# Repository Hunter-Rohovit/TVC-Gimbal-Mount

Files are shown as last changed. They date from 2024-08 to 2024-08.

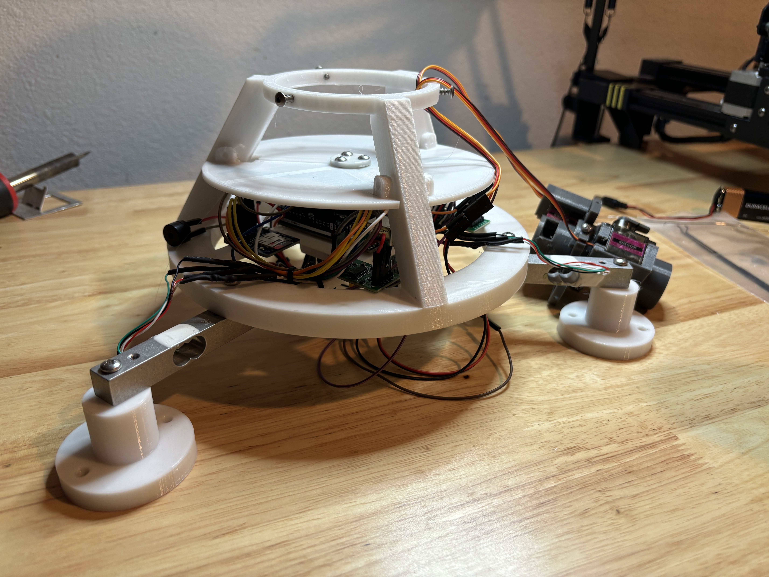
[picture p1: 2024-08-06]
TVC Mount Pics/ElectronicsShield(4).jpg

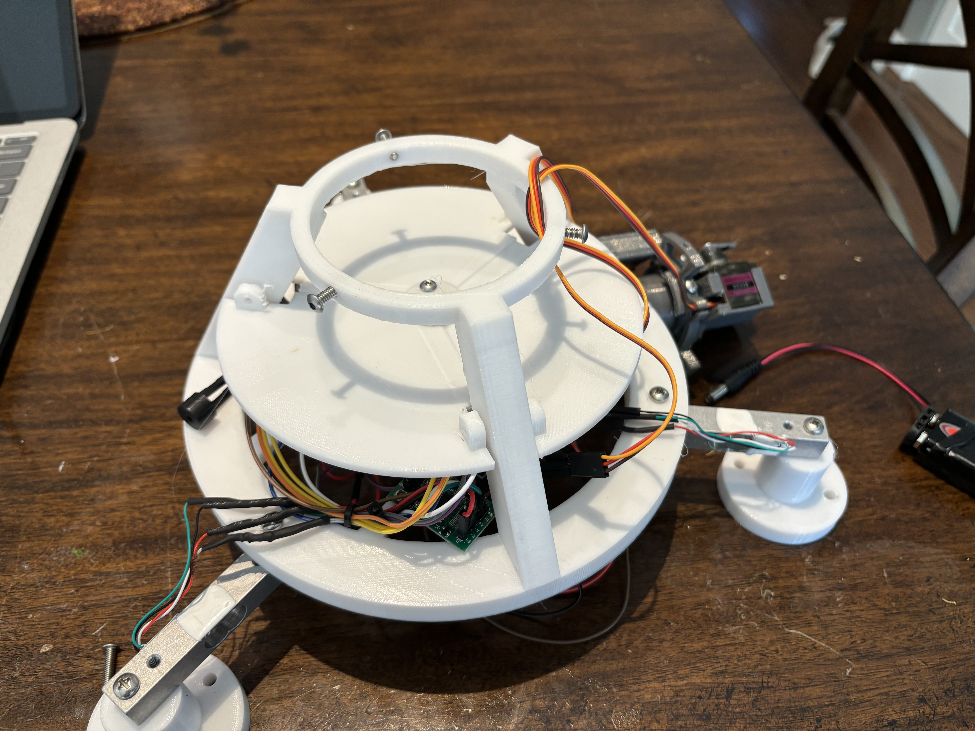
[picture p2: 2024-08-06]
TVC Mount Pics/ElectronicsShield.jpg

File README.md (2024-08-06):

# TVC-Gimbal-Mount
The TVC Gimbal Mount is an ongoing project with the eventual goal of creating a model rocket entirely controlled by TVC. This project was inspired by Joe Barnard @BPS.space, who attempted to land a model rocket using TVC. As for right now, the only goal is to achieve vertical controlled liftoff. The gimbal mount is designed using Autodesk Fusion360 to be 3D printed in three main pieces (outer layer, inner layer, motor casing). The current version is capable of 10 degrees of freedom. While designing an effective TVC mount is the main goal of the project, I am also gaining valuable experience with collecting data and performing data analysis on Static Fire tests. Most of the data being collected is thrust-force produced by the solid rocket motors through the use of load cells and HX711 amplifiers. This project ultimately is a culmination of all the skills I have learned so far and is purely my design: CAD, Arduino, Python. [Link to Onshape CAD model](https://cad.onshape.com/documents/d0d010f00d2c0b7870c7f789/w/7c25825be46c67b1ea6ad60a/e/3f60fee57cc94159316f0923)

## Static Fire Test


## TVC Mount


## CAD Design


## Data Analysis


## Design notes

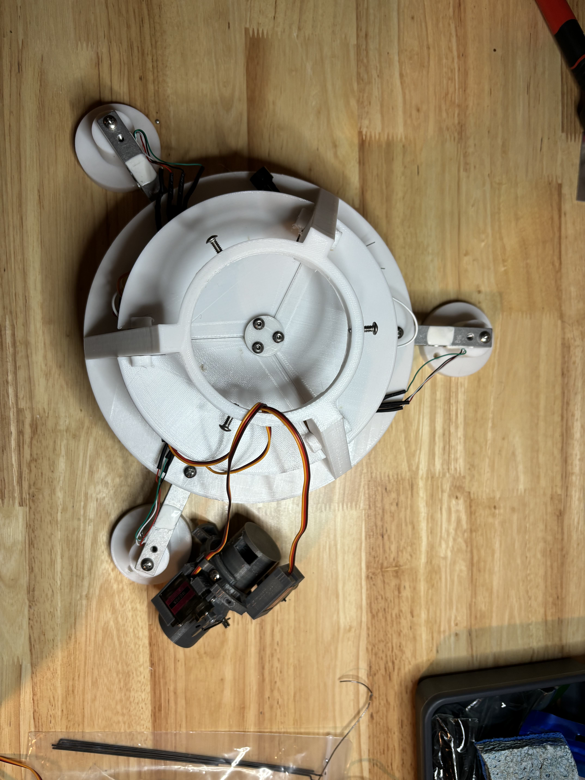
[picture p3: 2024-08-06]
TVC Mount Pics/ElectronicsShield(3).jpg

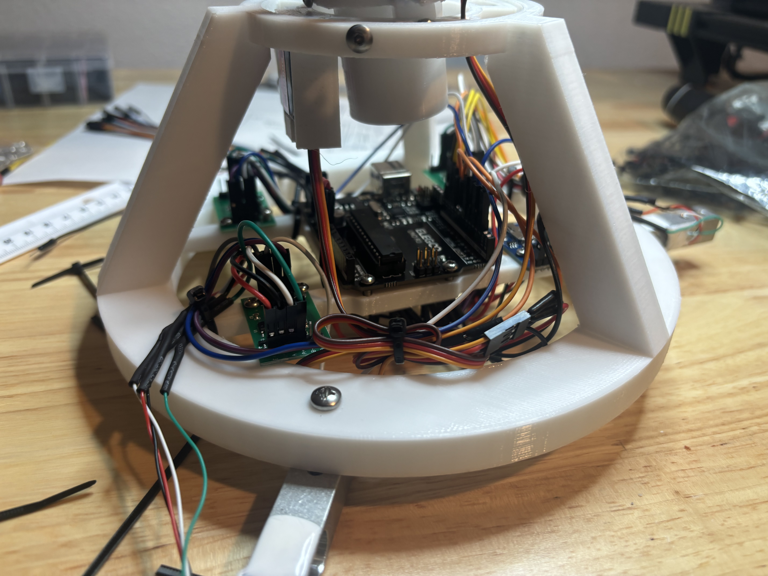
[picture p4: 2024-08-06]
TVC Mount Pics/Electronics(3).jpg

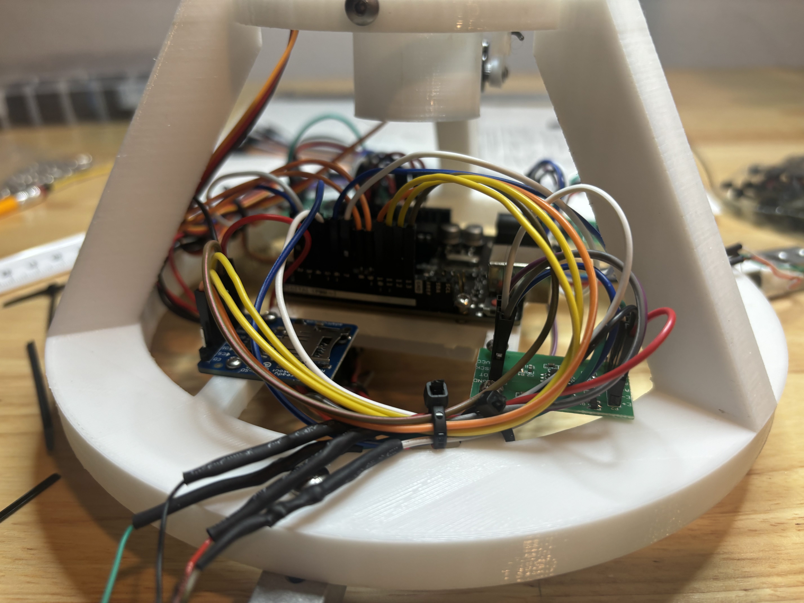
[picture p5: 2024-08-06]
TVC Mount Pics/Electronics(2).jpg

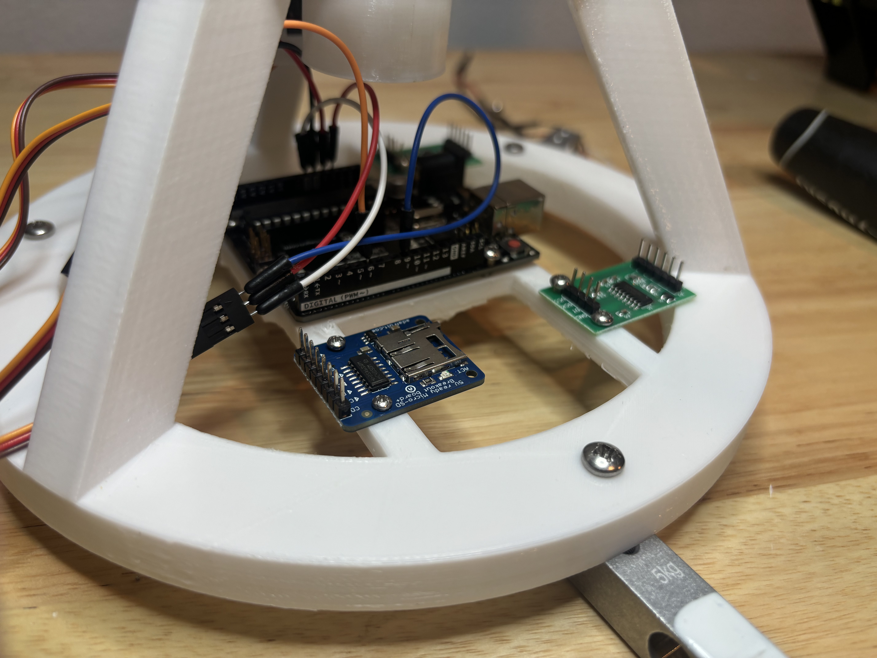
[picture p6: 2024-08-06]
TVC Mount Pics/Electronics(NotConnected).jpg

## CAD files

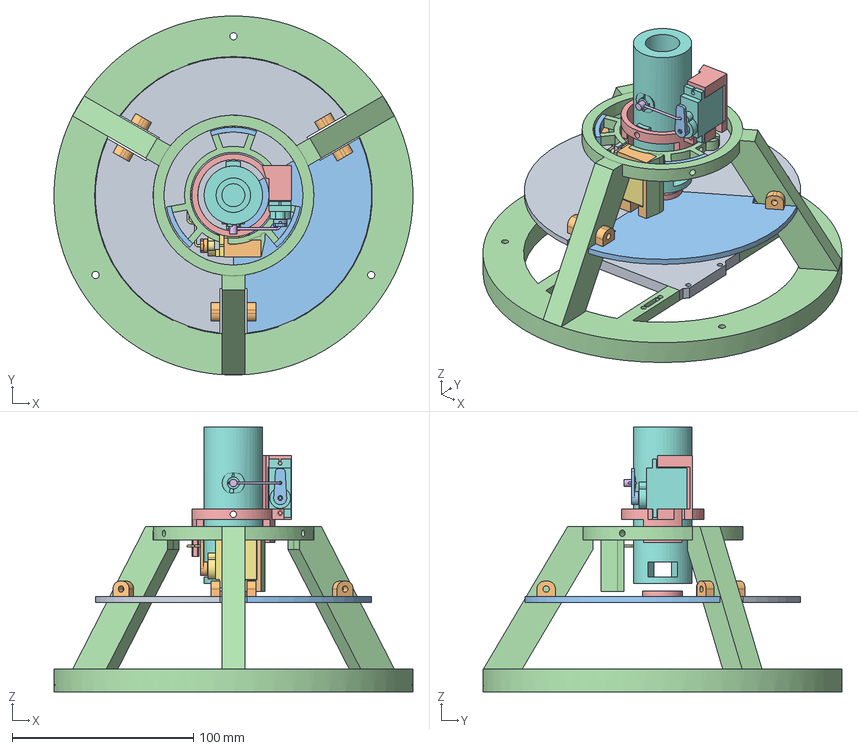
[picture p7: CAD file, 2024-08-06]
CADfiles/TVC_FullTestMount.step
197.9 x 197.9 x 146.1 mm
InnerLoop(Mirror)
InnerLoop
InnerLink
OuterLink\
C6-5 Engine Holder
ArduinoPlate
Thread
Thread (1)
ShieldPt2
Thread (2)
Thread (3)
StaticFireMount (1)
ShieldConnector
LinkageStopper
OuterServo
Thread (4)
InnerServo
Thread (5)
ShieldPt1
OuterControlHorn
InnerControlHorn

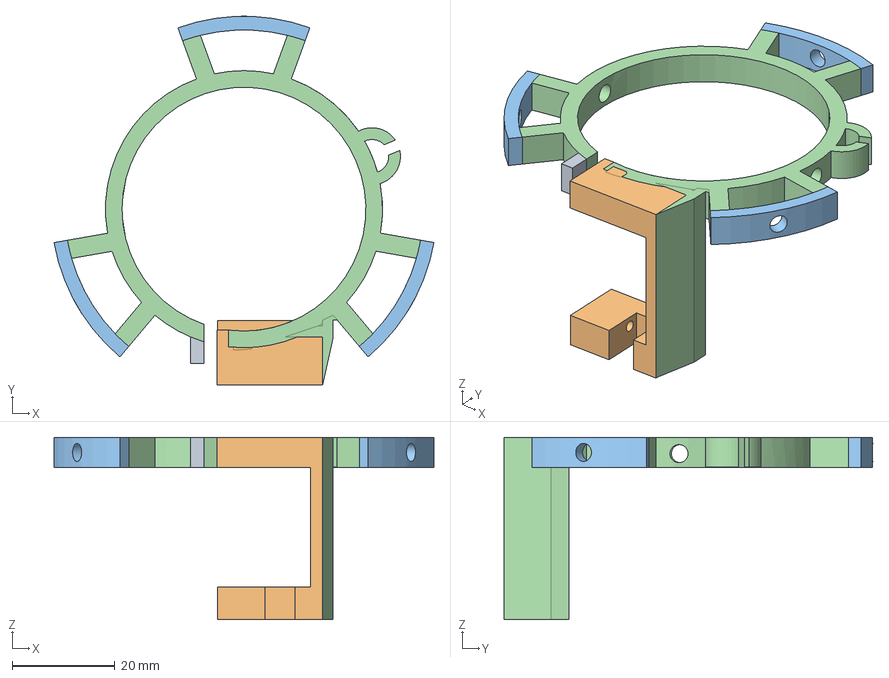
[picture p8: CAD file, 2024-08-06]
CADfiles/OuterLoop.step
73.8 x 71.6 x 35.4 mm
InnerLoop(Mirror)

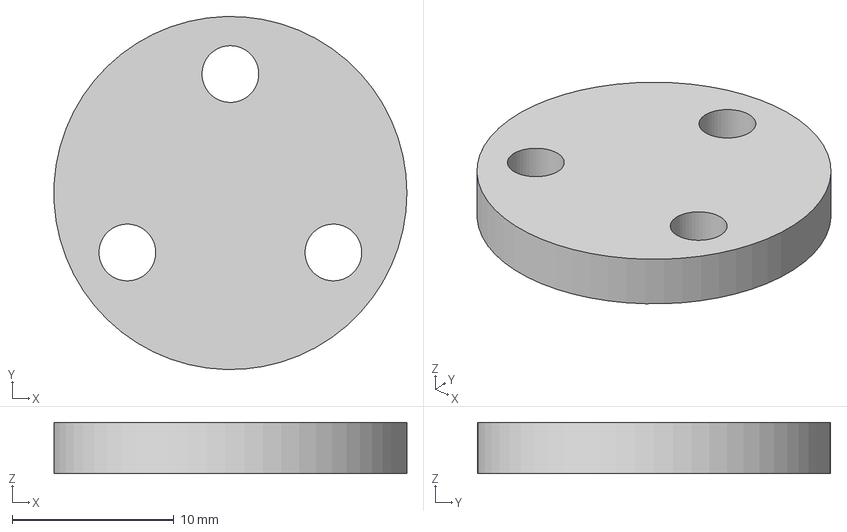
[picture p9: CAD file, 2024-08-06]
CADfiles/ShieldConnector.step
21.8 x 21.8 x 3.17 mm

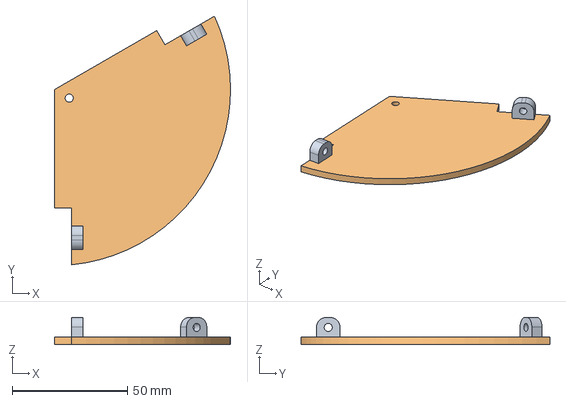
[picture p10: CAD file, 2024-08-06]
CADfiles/Electronics Shield.step
76.2 x 107.6 x 11.7 mm

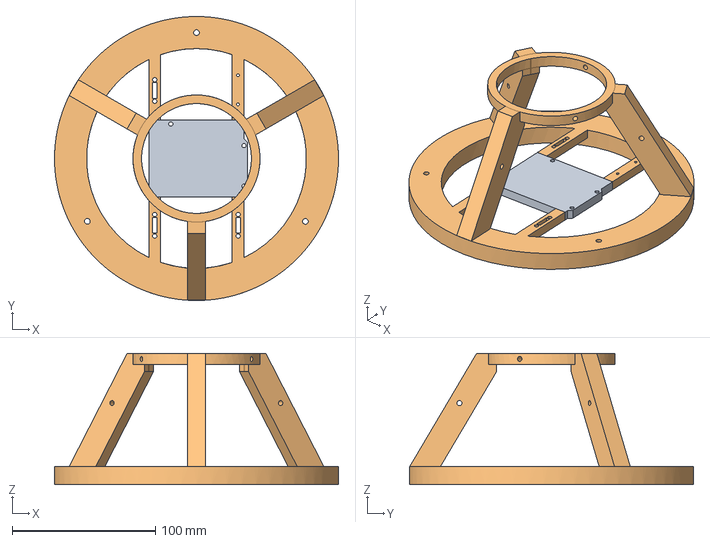
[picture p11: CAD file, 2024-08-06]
CADfiles/StaticFireMount.step
197.9 x 197.9 x 91.4 mm

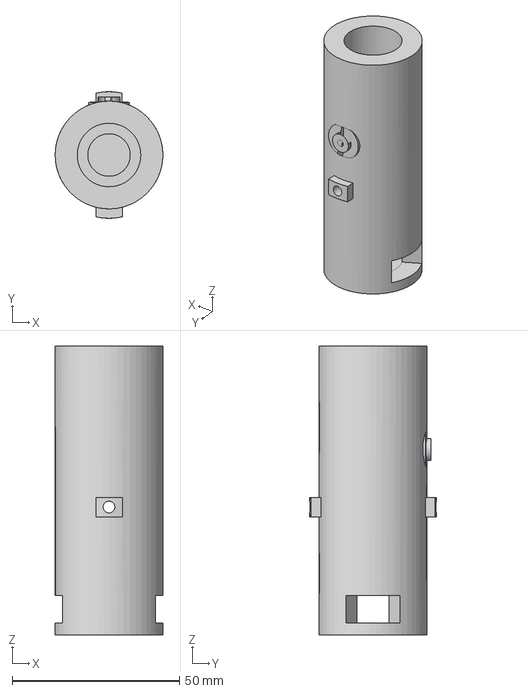
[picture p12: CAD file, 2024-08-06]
CADfiles/MotorHolder C6-5.step
32.2 x 37.8 x 86.4 mm

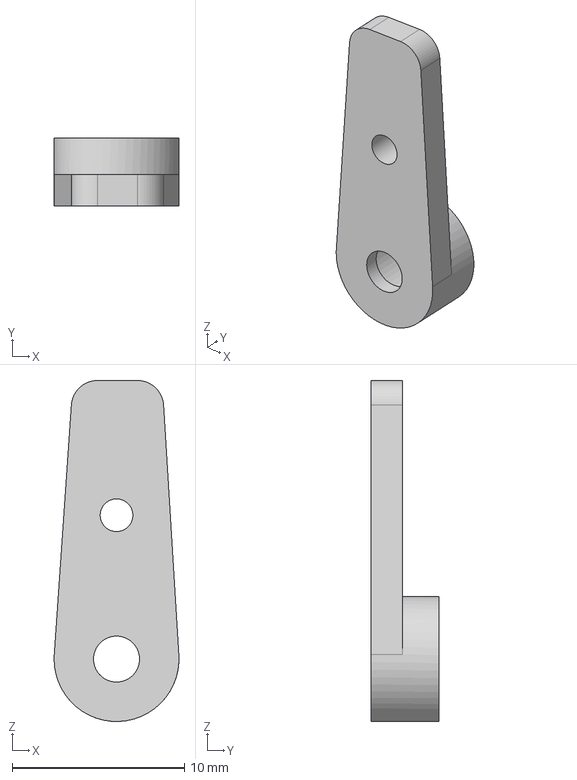
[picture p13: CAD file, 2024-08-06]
CADfiles/Control Horn Upper.step
7.25 x 3.96 x 19.8 mm

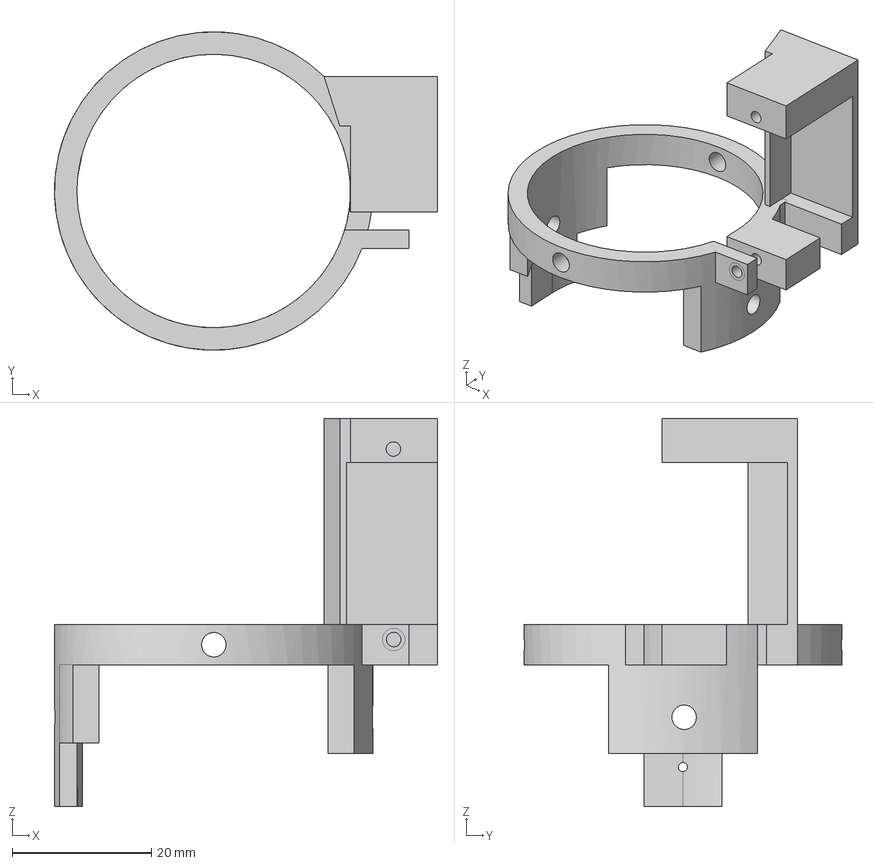
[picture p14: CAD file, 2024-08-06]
CADfiles/InnerLoop.step
55.0 x 45.7 x 55.8 mm

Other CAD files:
CADfiles/ControlHornLower.step

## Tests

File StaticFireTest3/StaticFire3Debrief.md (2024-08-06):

Static fire 3 was the most successful test so far. No critical errors involved. TVC mount control significantly improved compared to last test. Little to none unwanted movement with the outer servo. Likely a result of improvements with the TVC mount itself. Less stripped hinge damped any minor movements in the servo and smaller hole for servo link prevented any wiggle movement. Although there is still improvement to be made with servo control, this test showed positive signs. TVC stayed vertical when it was supposed to with little sporadic movement. The four corner gimbal worked very well again. After the mount completed its four corner gimbal, it returned to its original zero position. The total impulse (8.23N) was again lower than the expected impulse of 10N. I recalibrated the load cells using an actual scale compared with my previous weight of water method (poured 500ml of water into a cup on the scale and set the known weight to be 500g). To my surprise there wasn't a large difference in thrust values. However, my max thrust was significantly higher at 13.8N. At this point, I believe the lower thrust is not a result of improperly calibrated loadcells, but rather manufacturer's error in making the solid rocket motors. Another test might be needed to be confident with this assumption though.

Looking at the Thrust vs. time graph, the 80hz load cells again created a more detailed graph. The max thrust was at 13.82N, which is the highest so far. However, the total impulse was the lowest its been so far at 8.23N.

Looking at the scatterplot is where we find the most significant improvements from the test. The x-range was only 3.22cm and the y-range was 2.99cm. The fact that these two values are nearly identical and relatively small in magnitude shows that both the inner servo and the outer servo have good control of the motor holder. Compared to the last few tests where one of the ranges was always significantly greater than the other.

After Static Fire 3 I decided to improve the graphs/plots in DataPlotter.py through the use of animations. For the Thrust vs. time graphs I added a vertical line that shades in the graph as it moves from left to right. Although there isn't a very practical application to this vertical line, it is definitely more visually appealing. However, in the scatter plot showing the center of force, I decided to plot the points one-by-one with time. Now, it is easy to see how the center of force actually moved with respect to time. Because flight test 3 made use of the four corner gimbal, we can actually see the movement of the TVC in the scatter plot. The scatter plot creates a "diamond" shape, which makes sense as the TVC moved to four different corners. We can also see that after the "diamond" shape is created, data points are plotted at the center of the diamond, which aligns with the code moving the TVC mount back to the center or zero positions. Additionally, since the time of the scatter plot is aligned with the time of the Thrust graph, we can see that the four corners movement started at approximately 0.2s past the time where Thrust = 1N, which verifies the TVC code worked as intended. 

Overall, a very successful test. Greater control over thrust vectoring and systems working as intended. New changes to DataPlotter code provide better analysis of collected data. At this point, it is unlikely there will be any major changes to the TVC mount. Possibly minor changes to hinge width or servo link hole sizes. Minor changes to electronics and power distribution are also possible. Additionally, converting the electronics into a PCB is likely a next step for the static fire mount. However, after these past tests, it is likely I will begin working on the actual rocket itself and flight software to reach the ultimate goal of a thrust vector controlled rocket.  
<br>
<br>
Changes for test 4:<br>
-TBD <br>

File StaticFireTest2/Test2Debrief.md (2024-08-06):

Another successful test of the TVC mount without any critical errors involved. TVC mount didn't break this time as a result of increased strength from PETG and widened hinges. Ejection vents worked flawlessly and electronics shield prevented any flames from reaching the electronics beneath it. TVC mount struggled to stay vertical when it was supposed to. Lots of sporadic movement, mostly with the outer servo. The four corner gimbal worked very well (much better than I had anticipated). The TVC mount appeared to be more in control during gimbaling movements rather than during static positions. The force from the thrust didn't affect the servos ability to move the motor holder in both directions. The total impulse (8.54 N-s) was significantly lower than the expected impulse of 10 N-s. However, it was similar to the previous test of 8.76 N-s. I didn't recalibrate the load cells to see if the calibration factors were truly the issue. However, considering both tests had similar total impulse that were both lower than expected yield, I am confident that the load cells just need to be recalibrated. 

Looking at the Thrust vs. time graph, we can see the 80hz load cells provided a much cleaner and more detailed graph than the 10hz load cells (obviously 8 times the amount of data would do this). This time max thrust was 11.175N which is more than the previous test's. However, because the last test was recorded at 10hz it is likely the true max wasn't recorded in the data. After the initial peak thrust, there is constant thrust at around 4N for the next 1.6 seconds. Once again, this graph matches up with the manufacturer's data. 

Looking at the scatterplot, we can visibly see that the TVC mount was less controllable during this test. The max Y-range was 67.5cm, which is definitely a recording error as the max it can be is 14cm. More analysis of the data is needed to get rid of outlier data. The range in the X-direction was 6cm which is reasonable. The excessively large range in the y-direction shows the lack of control with the outer loop. Considering the servo pulls on the inner loop with a larger lever arm, the servo has to move significantly less to move the mount the same number degrees as compared with the inner servo which pulls directly on the motor holder. 

Considering the changes that were made with test 2 and the sporadic movement of the servos that wasn't seen with test 1, it is safe to say the movement has to do with changing the HX711 boards from 10hz to 80hz. These boards pull significantly more current than they did in test 1 leaving the servos with insufficient power. I attempted to resolve this issues in multiple ways. The first was adding a power supply solely for powering the servos. This improved the servos' ability to gimbal, but it didn't prevent the sporadic movement during static holds. (I made sure to connect the power supply's ground to the Arduino's ground, so as to have a common ground) The next idea I had was to connect a 1000uF capacitor in parallel with the servos' power and ground wires. I figured the capacitor's ability to store charge would help smooth the current creating a more stable TVC mount, but nothing changed after implementing this. I tried replacing the motors, which did help a little bit, but not much. I also made sure the 9V batteries that were used were full, but that also had little effect. In conclusion, I am not sure how to move forward with making the TVC mount more stable. But, I'm fairly confident it is a power distribution issue rather than a mechanical or coding error. 
<br>
<br>
Changes for test 3: <br>
-recalibrated load cells <br>
-Smaller hole size for outer servo link<br>
-less stripped outer hinge<br>

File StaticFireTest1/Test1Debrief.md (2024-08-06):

Overall a successful first test. TVC mount stayed vertical throughout the duration of the test. Successful readings from load cells and writing data to SD cards. Comparing the test data to the manufacture's data showed a similar shape of a graph, with peak thrust around 0.2 seconds after ignition and relatively constant thrust for 1.6 seconds. The total impulse (8.76 N-s) was significantly lower than theoretical yield (10 N-s) likely due to incorrect calibration factors (need to recalibrate the load cells again to verify factors).

Looking at the scatterplot which maps out the center of force (akin to center of except with thrust instead of mass) for every data point taken by the loadcells, an apparent trend emerges. First, the TVC mount is relatively stable in the Y-direction. The Y-axis is controlled by the upper (or inner) servo directly connected to the motor holder. It was apparent when completing motion tests that this servo had significantly more control over its position compared to its counterpart servo. The range for the CF's Y position was 0.6213cm, compared to the range for the CF's X position which was 2.0751cm. Will keep this in mind for future versions of the TVC mount. However, this will not be changed for the next test.  

Additionally, the loadcells currently have a data logging rate of 10hz. After looking at the specifications of HX711 module, I inquired that it is possible to increase this rate to 80hz. While 10hz provides data to graph the thrust vs. time, we only obtain 20 total data points over the duration of the test. If we change this to 80hz, we can obtain 160 data points, providing a more accurate representation of the test. This will be changed for the next test. 

Turns out I can't ignore the ejection charge. Explosion at the end of the video was due to the ejection charge which sent the engine flying up into the air. I considered removing the ejection charge from the rocket engine, but due to safety concerns I will opt for a different option. Buying C6-0 engines is a difficult task as Estes produces very few of them. The other option which I will implement in Static Fire Test 2 is giving the rocket engine holder two side vents. The side vents at the bottom of the holder will allow pressure from the ejection charge to escape out the sides and shouldn't result in an airborne rocket engine. 

While writing this debrief initially, there didn't appear to be any significant damage to the TVC mount after testing. After further inspection it became clear that the outer loop of the TVC mount broke at its hinge. Before the test this was a major area of concern as the hinge wasn't solidly connected to the TVC mount. To correct this issue, the areas around the hinge will be widened to give it more support. Additionally, the PLA filament that was used for V1 will be replaced with PETG filament (a stronger variant of plastic) for V2.
<br>
<br>
Changes for test 2:<br>
-10hz to 80hz data log rate <br>
-side vents in engine holder<br>
-Recalibrated load cells<br>
-PLA to PETG<br>
-Widened hinges<br>
-Added Electronics Shield (see Ejection Vent Test)<br>
-Test Engine Gimbal (Max Corners)<br>

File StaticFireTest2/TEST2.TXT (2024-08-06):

Setting TVC to zero positions...
Beginning Tare...
Continuing with final countdown...
T-10
T-9
T-8
T-7
T-6
T-5
T-4
T-3
T-2
T-1
Ignition
Force in Newtons: 
-0.0013908524 -0.0002744333 0.0020747354 
-0.0041228837 -0.0000997939 0.0022247166 
-0.0015398724 0.0023451576 0.0007749013 
-0.0026326849 0.0053639245 0.0037495226 
-0.0015647090 0.0029439210 0.0023497006 
0.0007947728 -0.0014719605 0.0012998343 
0.0013411791 0.0019958786 0.0058992481 
0.0021359519 0.0032183547 0.0050243606 
0.0030052347 0.0029439210 0.0018997579 
0.0016143822 0.0013222696 0.0025996687 
0.0019620954 0.0008482485 0.0040744810 
0.0011424860 0.0015717548 0.0036495351 
-0.0005215697 0.0025696940 0.0044994263 
-0.0023098084 0.0030686635 0.0049243721 
-0.0028313781 0.0050645427 0.0032245893 
-0.0006954263 0.0093307323 -0.0038745064 
-0.0022601351 0.0129732120 -0.0071240911 
-0.0143555831 0.0487992334 -0.0194975147 
-0.0248366498 -0.0329818964 0.0175227665 
0.0345726203 -0.0503460454 0.0308960652 
0.0149268269 0.0078837208 -0.0044744296 
-0.0107294332 0.1841447639 -0.0846892070 
-0.1168067693 0.1877124023 -0.0927131843 
-0.1902984237 -0.0689576148 0.0467940330 
-0.0095869483 -0.1940742683 0.0350205373 
0.2214436054 -0.2574434280 0.1679286003 
0.1481009578 -0.0996941471 0.0897885608 
0.0988001918 0.1000933170 -0.0716658687 
0.0044457607 0.2283534765 -0.1199847221 
-0.1451702213 0.0777145338 -0.0576676559 
-0.1272381663 -0.0818060874 0.0483938312 
0.0184784679 -0.2273056507 0.1301334142 
0.1571663379 -0.2188730716 0.1374324798 
0.1023518443 -0.0367740678 0.0528932571 
-0.0407817792 0.1039852857 -0.0600173521 
-0.0519831132 0.1246675848 -0.0590674781 
-0.0490275478 0.1119189023 -0.0449692726 
-0.0833021354 0.0657891559 -0.0078489995 
-0.0510393142 0.0220544624 0.0025996687 
0.0035764777 0.1801031208 -0.1397071952 
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

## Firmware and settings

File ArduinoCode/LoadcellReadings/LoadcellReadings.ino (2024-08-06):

#include "HX711.h"

//L1 (6,7) = 394.86
//L2(2,3) = -393.09
//L3(4,5) = 392.33
#define calibration_factor_1 394.86
#define calibration_factor_2 393.09
#define calibration_factor_3 392.33

#define LOADCELL_1_DOUT_PIN  6
#define LOADCELL_1_SCK_PIN  7

#define LOADCELL_2_DOUT_PIN  5
#define LOADCELL_2_SCK_PIN  4

#define LOADCELL_3_DOUT_PIN  3
#define LOADCELL_3_SCK_PIN  2

HX711 LoadPoint1;
HX711 LoadPoint2;
HX711 LoadPoint3;

void setup() {
  Serial.begin(9600);
  Serial.println("LoadPointMeasurements");

  LoadPoint1.begin(LOADCELL_1_DOUT_PIN, LOADCELL_1_SCK_PIN);
  LoadPoint1.set_scale(calibration_factor_1); 

  LoadPoint2.begin(LOADCELL_2_DOUT_PIN, LOADCELL_2_SCK_PIN);
  LoadPoint2.set_scale(calibration_factor_2);

  LoadPoint3.begin(LOADCELL_3_DOUT_PIN, LOADCELL_3_SCK_PIN);
  LoadPoint3.set_scale(calibration_factor_3);
  Serial.println("Beginning Tare: ");
  LoadPoint1.tare();
  LoadPoint2.tare();
  LoadPoint3.tare();

  Serial.println("Readings:");
  int i=0;
  while(i<800){
    Serial.print("Load 1: ");
    Serial.print(LoadPoint1.get_units(), 1); 
    Serial.print(" g"); 
    Serial.print("________________");
    Serial.print("Load 2: ");
    Serial.print(LoadPoint2.get_units(), 1); 
    Serial.print(" g"); 
    Serial.print("________________");
    Serial.print("Load 3: ");
    Serial.print(LoadPoint3.get_units(), 1); 
    Serial.print(" g"); 
    Serial.print("________________");
    Serial.println();
    i++;
  }
}

void loop() {
  
}

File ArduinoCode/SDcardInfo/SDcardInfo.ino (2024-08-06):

// include the SD library:
#include <SPI.h>
#include <SD.h>

// set up variables using the SD utility library functions:

Sd2Card card;

SdVolume volume;

SdFile root;

// change this to match your SD shield or module;
// Default SPI on Uno and Nano: pin 10
// Arduino Ethernet shield: pin 4
// Adafruit SD shields and modules: pin 10
// Sparkfun SD shield: pin 8
// MKRZero SD: SDCARD_SS_PIN

const int chipSelect = 10;

void setup() {

  // Open serial communications and wait for port to open:

  Serial.begin(9600);

  while (!Serial) {

    ; // wait for serial port to connect. Needed for native USB port only

  }

  Serial.print("\nInitializing SD card...");

  // we'll use the initialization code from the utility libraries

  // since we're just testing if the card is working!

  if (!card.init(SPI_HALF_SPEED, chipSelect)) {

    Serial.println("initialization failed. Things to check:");

    Serial.println("* is a card inserted?");

    Serial.println("* is your wiring correct?");

    Serial.println("* did you change the chipSelect pin to match your shield or module?");

    while (1);

  } else {

    Serial.println("Wiring is correct and a card is present.");

  }

  // print the type of card

  Serial.println();

  Serial.print("Card type:         ");

  switch (card.type()) {

    case SD_CARD_TYPE_SD1:

      Serial.println("SD1");

      break;

    case SD_CARD_TYPE_SD2:

      Serial.println("SD2");

      break;

    case SD_CARD_TYPE_SDHC:

      Serial.println("SDHC");

      break;

    default:

      Serial.println("Unknown");

  }

  // Now we will try to open the 'volume'/'partition' - it should be FAT16 or FAT32

  if (!volume.init(card)) {

    Serial.println("Could not find FAT16/FAT32 partition.\nMake sure you've formatted the card");

    while (1);

  }

  Serial.print("Clusters:          ");

  Serial.println(volume.clusterCount());

  Serial.print("Blocks x Cluster:  ");

  Serial.println(volume.blocksPerCluster());

  Serial.print("Total Blocks:      ");

  Serial.println(volume.blocksPerCluster() * volume.clusterCount());

  Serial.println();

  // print the type and size of the first FAT-type volume

  uint32_t volumesize;

  Serial.print("Volume type is:    FAT");

  Serial.println(volume.fatType(), DEC);

  volumesize = volume.blocksPerCluster();    // clusters are collections of blocks

  volumesize *= volume.clusterCount();       // we'll have a lot of clusters

  volumesize /= 2;                           // SD card blocks are always 512 bytes (2 blocks are 1KB)

  Serial.print("Volume size (Kb):  ");

  Serial.println(volumesize);

  Serial.print("Volume size (Mb):  ");

  volumesize /= 1024;

  Serial.println(volumesize);

  Serial.print("Volume size (Gb):  ");

  Serial.println((float)volumesize / 1024.0);

  Serial.println("\nFiles found on the card (name, date and size in bytes): ");

  root.openRoot(volume);

  // list all files in the card with date and size

  root.ls(LS_R | LS_DATE | LS_SIZE);

  root.close();
}

void loop(void) {
}
